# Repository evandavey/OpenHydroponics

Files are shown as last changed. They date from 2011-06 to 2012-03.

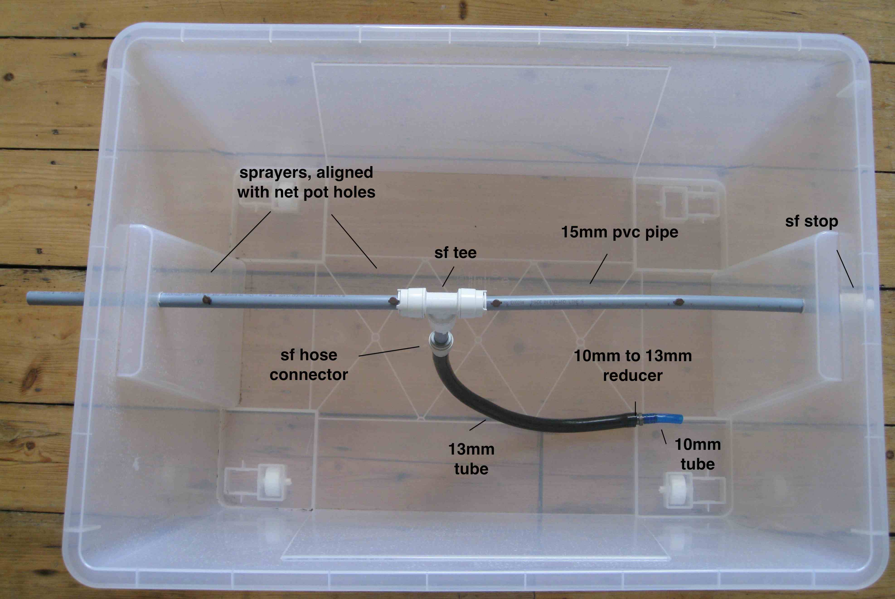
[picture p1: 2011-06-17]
.solderpad/photo.jpg

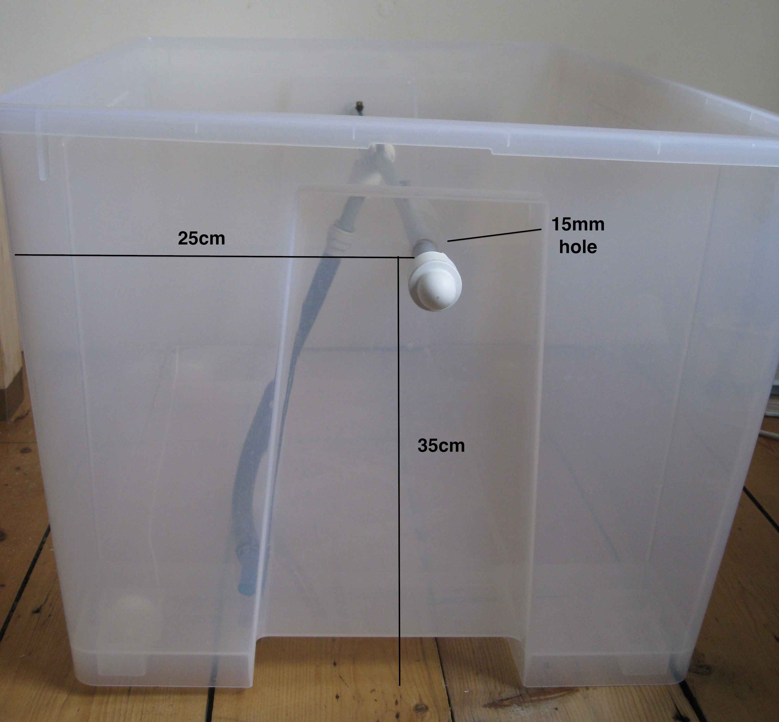
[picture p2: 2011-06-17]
docs/prototype_images/side_w_pipe_hole.jpg

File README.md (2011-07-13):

#OpenHydroponics

An open hardware project for hydroponics.

* firmware
	- arduino pump controller sketch

* hardware
	- Eagle circuit schematic for pump controller

* 3dmodels
	- sketchup model of aeroponics prototype

* docs
	- build documentation for aeroponics prototype

* python
	- python code to interface with the pump controller via serial

* processing
	- processing code to create a gui that interfaces with the conroller via serial

#Contributors

* Evan Davey, evan.j.davey@gmail.com

#License

* See LICENSE.txt

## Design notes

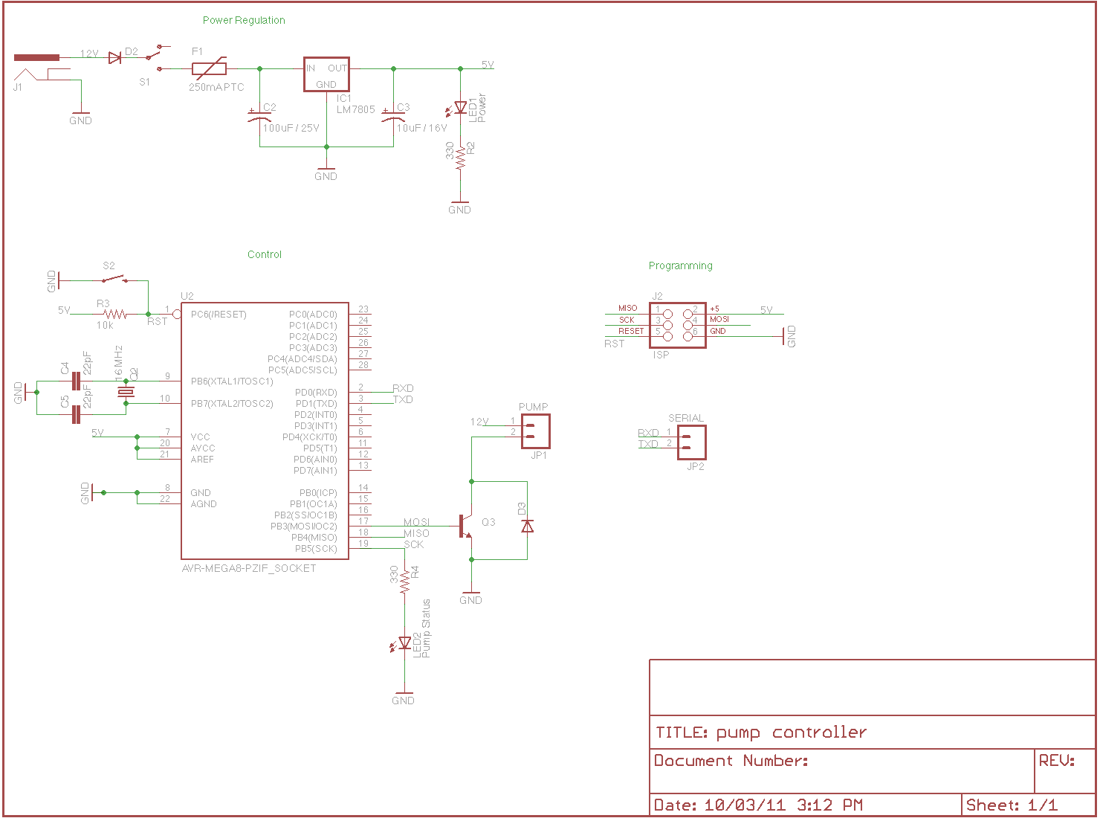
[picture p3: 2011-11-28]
.solderpad/schematic.png

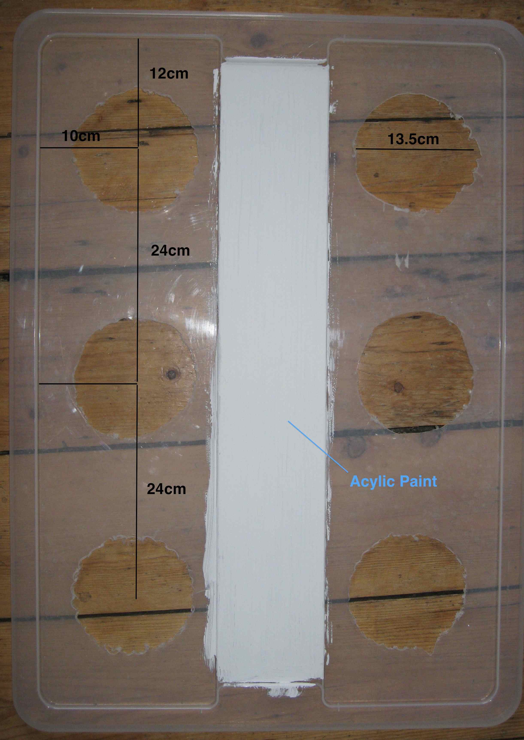
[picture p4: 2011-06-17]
docs/prototype_images/lid_w_annotation.jpg

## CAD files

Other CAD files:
3dmodels/sketchup_aeroponicsmodel.skp

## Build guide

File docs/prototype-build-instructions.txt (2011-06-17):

Title: Aeroponics Prototype System

#Introduction
This document describes how to build an aeroponics system that can be used for indoor growing.

#Why Hydroponics
Hydroponics is a viable alternative to soil-based growing, particularly indoors, for a number of reasons:

* soil is messy indoors
* hydroponics can produce excellent growing results through precise control over plant nutrients
* hydroponics is water-efficient 

There are a number of different hydroponics methods. This build uses aeroponics where the plant's roots are sprayed regularly with a fine mist of nutrient rich solution.  This method can produce excellent results since the spraying process introduces significant oxygen and is targeted directly to the roots.  The downside of the method is that it is more complex and energy inefficient.

#Parts List
* a plastic container with lid, [ikea salma][],[ikea salma lid][]
* approx. 50cm of 13mm irrigation hose, [growing-life][]
* 4 aeroponics spray nozzles, [growing-life][]
* 6 140mm heavy duty net pots, [growing-life][]
* approx. 1m of 15mm pvc pipe, [jw-hinton][]
* 2 sf pvc end caps, [jw-hinton][]
* 1 sf pvc tee connector, [jw-hinton][]
* 1 pvc hose connector, [jw-hinton][]
* 6 15mm sf inserts, [jw-hinton][]
* 1 13mm to 10mm reducer, [water-cooling-shop][]
* approx. 10cm of 10mm hose, [water-cooling-shop][]
* 1 12VDC pump [quality-gadgets-ebay][]

#Build
1. Drill or cut 6x140mm holes in the plastic tub lid.  For the Ikea Salma lid, there are two panels which should have 3 holes each.  They should be placed 10cm from the long edge and at 12cm,36cm and 60cm from the left short edge. 
2. Test that the net pots fit the holes snugly and adjust to fit.
3. Drill a 15mm hole in each side of the tub so that the pvc pipe can be inserted long ways through the tub.  Holes should be 35cm from the bottom and 25cm from the left edge.
4. Cut a 90cm length of pvc pipe and then cut this in half.  Cut a separate 5cm length of pipe.  Insert each end of the pipes into the tee connector using the inserts.  Connect the 5cm pipe to the hose connector then insert into the base of the tee connector. Insert the connected pipe into the plastic tub.  With the lid on, mark the pvc for the best location of the sprayers by aligning them with the net pot holes, drill pilot holes then connect the sprayers.  Place the stop ends on each end of the pvc pipes once the sprayers have been inserted.
5. Cut a small length of 10mm pipe and use this with the  10mm to 13mm reducer to connect to the pump.  Cut a small section of 13mm hose and use this to connect the 13mm reducer end to the hose connector.
6. Fill with a small amount of water then connect the pump directly to the 12v power supply to test.
7. Paint the tub and lid (a primer coat may be required).  This is so light is kept away from the roots / nutrients solution.
8. Move the system to its final location (eg: at a window for sunlight). Fill the tub with a nutrient solution and add a grow medium (eg: perlite) to the net pots. 

[quality-gadgets-ebay]: http://cgi.ebay.co.uk/ws/eBayISAPI.dll?ViewItem&item=190473725204
[water-cooling-shop]: http://www.thewatercoolingshop.co.uk/
[growing-life]: http://www.growing-life.com/
[jw-hinton]: http://www.jwhinton.co.uk/
[ikea salma]: http://www.ikea.com/gb/en/catalog/products/70102972
[ikea salma lid]: http://www.ikea.com/gb/en/catalog/products/90110301

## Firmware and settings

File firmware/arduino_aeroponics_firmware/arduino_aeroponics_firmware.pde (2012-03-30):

/* Hydroponics System 

-- Aeroponics controller
-- Author: Evan Davey, evan.j.davey@gmail.com

--V1.1
--- adds string array for state labels
--- converts data string to json from csv
--- implements a newState variable to allow state change events
--- sends data string on state changes
--- adds a name variable to identify devices

Cycles a pump for use in a hyrdoponics system
Implemented as a state machine 
X-valid serial command 
      *menu -> send main menu
      *data -> send data
      **rst -> state 3 
0-idle 
  Outputs: pumpCtrl=Low,statusLed=Blink,reset=Low
  off timer ends -> state 1
  waterSensor=High -> state 2
  
1-pumping
  Outputs: pumpCtrl=High,statusLed=Low,reset=Low
  on timer ends -> state 1
  waterSensor=High -> state 2
  
2-error,water low
  Outputs: pumpCtrl=Low,statusLed=fast blink,reset=Low
  requires reset to leave this state

3-reset
  Outputs: pumpCtrl=Low,statusLed=Low,reset=High
  Waits delay_time before resetting


*/


// hardware
const int pumpCtrl = 2; //connect via a transistor with back voltage protection
const int statusLed = 13; //connect using a current limiting resistor
const int reset = 12; //connect to reset via a transistor tied to ground
const int waterSensor = 8; //connect to a normally closed float switch
const int manualButton = 3;

// firmware defaults
const float vers=1.1;
char* name="Aeroponics 1";
const unsigned long default_pump_on_time = 30000; //on 30 seconds 
const unsigned long default_pump_off_time = 300000; //off 5 minutes
const long baud_rate=115200; //baud rate for serial 
volatile int debug_mode=0; //when high, outputs status data 
int pumpCycles = 1; //counter of pump cycles
int reset_delay=4; //time to wait after reset command issued
int start_state=0; //starting state
char* stateStrings[]={"0 - Idle","1 - Pumping","2 - Error, Water too low","3 - Waiting to reset","4 - Manual Mode"};
 

// 0 - idle
// 1 - pumping
// 2 - error, water level
// 3 - waiting for reset
volatile int currentState = -1;
volatile int newState = -1;




// Variables will change:
int ledState = LOW;             // ledState used to set the LED
int pumpState = LOW;             // ledState used to set the LED
long pumpTimer = 0; // will store last time LED was updated
int waterSensorState = LOW;
int manualButtonState = LOW;

volatile char cmd='-1';
long pump_on_time; //on 30 seconds 
long pump_off_time; //off 5 minutes
unsigned long previousMillis = 0;
boolean in_menu=false;


void setup() {


  pinMode(pumpCtrl, OUTPUT);
  pinMode(statusLed, OUTPUT);
  pinMode(reset, OUTPUT);
  pinMode(waterSensor, INPUT);
  pinMode(manualButton, INPUT);

  pump_off_time=default_pump_off_time;
  pump_on_time=default_pump_on_time;

  Serial.begin(baud_rate);

  //delay(1000);


  attachInterrupt(1, button1, RISING);

  newState=start_state;


}

void keepTime() {
   //keep the time
  unsigned long currentMillis = millis();
  pumpTimer += currentMillis-previousMillis;
  previousMillis = currentMillis;
  
 
  
}

void mainControlLoop() {
  
  keepTime();
  
  //check for errors
  errorCheck();
  
  //handle state
  handleState();

  
}


void loop()
{

  mainControlLoop();
  
  //in the main menu
  if (in_menu) {
    menu_main();
  }
 
  //process received serial data
  //available command *menu
  handleSerialIn();

  if (debug_mode && !in_menu) {


    if (pumpTimer % 5000 == 0) {
      Serial.println(":: DBEUG ::");
      status_toString();
    }
  } 

}


void handleSerialIn() {


  if ( Serial.available() > 0) { // if there are bytes waiting on the serial port

    char inByte = Serial.read(); // read a byte
    if (inByte == '*') { // if that byte is the desired character

      int len = 5; // expected string is 6 bytes long
      char inString[len]; // declare string variable
      for (int i = 0; i < len; i++) {
        inString[i] = Serial.read();
        delay(100);
      }

      //Serial.println(inString);

      if ( strstr(inString, "menu") != NULL ) { // check to see if the respose is "reset"
          menu_main(); 
      } else if (strstr(inString, "data") != NULL ) {

        //send data
        data_toString();

      } else if (strstr(inString, "*rst") != NULL ) {

        Serial.println("Resetting..");
        //send data
        newState=3;

      } else if (strstr(inString, "sone") != NULL ) {

        //Serial.println("Changing state to 1");
        //send data
        pumpTimer=0;
        newState=1;
        Serial.flush();

      } else if (strstr(inString, "stwo") != NULL ) {

        //send data
        newState=2;
        Serial.flush();

      } else if (strstr(inString,"idle") != NULL ) {

        //send data
        newState=0;
        pumpTimer=0;
        Serial.flush();


     }
    }
  }
}


void state_change() {
 
   data_toString(); 
  
}

void handleState() {
  
  if (newState!=currentState) {
    currentState=newState;
    state_change();
  }

  switch(currentState) {
    //IDLE
  case 0:

    flashLed(statusLed,1,1000);
    digitalWrite(pumpCtrl,LOW);
    //pump off timer exceeded, switch to pumping state
    if (pumpTimer >= pump_off_time) {
      pumpTimer=0;
      pumpCycles++;
      newState=1;
    }
    break;

    //PUMPING
  case 1:


    digitalWrite(pumpCtrl,HIGH);
    //pump on timer exceeded, switch to idle state
    if (pumpTimer >= pump_on_time) {
      pumpTimer=0;
      newState=0;
    }
    break;
    
 
    //ERROR
  case 2:
    digitalWrite(pumpCtrl,LOW);
    flashLed(statusLed,3,100);
    break;

    //RESET
  case 3:
  
   
    
    for (int i=reset_delay;i>0;i--) {
      Serial.print("Will reset in ");
      Serial.print(i);
      Serial.println("s");
      delay(1000);
    }
    
    Serial.println("** Resetting now **");
    digitalWrite(reset,HIGH);
    newState=0;
    break;

  //MANUAL ON
 
   case 4:
    digitalWrite(pumpCtrl,HIGH);
    break;

  default:
    break;

  }      


}

void data_toString() {


  
  
  //delay(1000);
  Serial.print("{");
  
  Serial.print("\"State\"");
  Serial.print(":");
  Serial.print(currentState);
  Serial.print(",");
  
   Serial.print("\"State Description\"");
  Serial.print(":");
  Serial.print(stateStrings[currentState]);
  Serial.print(",");
  
  Serial.print("\"Pump Timer\"");
  Serial.print(":");
  Serial.print(pumpTimer/1000);
  Serial.print(",");
  
  Serial.print("\"Pump Off Time\"");
  Serial.print(":");
  Serial.print(pump_off_time);
  Serial.print(",");
  
  Serial.print("\"Pump On Time\"");
  Serial.print(":");
  Serial.print(pump_on_time);
  Serial.print(",");
  
  Serial.print("\"Pump Cycles\"");
  Serial.print(":");
  Serial.print(pumpCycles);
  Serial.print(",");
  
  Serial.print("\"Water Sensor\"");
  Serial.print(":");
  Serial.print(waterSensorState);
  Serial.print(",");
  
  Serial.print("\"Name\"");
  Serial.print(":");
  Serial.print("\"");
  Serial.print(name);
  Serial.print("\"");
  Serial.print(",");

  Serial.print("}");
  
  Serial.println("");


}


void errorCheck() {

  // water level too low, enter error state
  if (!checkWater()) {
    newState=2; 
    return;
  } 





}


//checks the water sensor and returns true if water is present
boolean checkWater() {

/*  waterSensorState=digitalRead(waterSensor);

  if (waterSensorState == HIGH) {
    return false;
  } 
  else {
    return true;
  }
 
*/
 return true;

}

void state_toString(int state) {

  
  Serial.println(stateStrings[state]);
 

}

void status_toString() {

  Serial.print("Version: ");
  Serial.println(vers);
  Serial.print("Debug Mode: ");
  Serial.println(debug_mode);
  Serial.print("State: ");
  state_toString(currentState);
  Serial.print("Pump Timer: ");
  Serial.println(pumpTimer/1000);
  Serial.print("Pump Cycles: ");
  Serial.println(pumpCycles);
  Serial.print("Pump Off Time: ");
  Serial.println(pump_off_time/1000);
  Serial.print("Pump On Time: ");
  Serial.println(pump_on_time/1000);
  Serial.print("Water Sensor: ");
  Serial.println(waterSensorState); 

}

void menu_show() {

  Serial.println("::::: HYDRO SYSTEM :::::");
  status_toString();
  delay(500);
  Serial.println("--------------------------------");
  Serial.println("(1) - exit menu");
  Serial.println("(2) - reset");
  Serial.println("(3) - toggle debug");
  Serial.println("(4) - force state");
  Serial.println("(5) - set pump on time");
  Serial.println("(6) - set pump off time");

}

void menu_main() {


  //first time in, show the menu
  if (!in_menu) {
    delay(700);
    Serial.flush();
    menu_show();
    in_menu=true;
  }


  //wait for command
  if (in_menu) {

    if ( Serial.available() > 0) { // if there are bytes waiting on the serial port

      cmd = Serial.read();

      switch (cmd) {

      case '1':
        Serial.println("exiting menu");
        in_menu=false;
        break;

      case '2':

        in_menu=false;
        newState=3;
        break;

      case '3':
        in_menu=false;
        debug_mode=!debug_mode;
        Serial.print("Debug mode=");
        Serial.println(debug_mode);
        break;

      case '4':


        Serial.println("States-");
        for (int i=0;i<=3;i++) {
          state_toString(i);
        }
        Serial.print("State Number (0-3): ");

        Serial.flush();
        while (true) {
          //ensure operation continues while waiting
          mainControlLoop();
          if ( Serial.available() > 0) { // if there are bytes waiting on the serial port
            char * cmd_c="0";
            cmd_c[0]=Serial.read();

            int cmd_i=atoi(cmd_c);

            if (cmd_i<=3) {
              Serial.print("Setting state to: ");
              Serial.println(cmd_i);
              pumpTimer=0;
              newState=cmd_i;
              in_menu=false;
              break;
            } 
            else {

              Serial.print("State Number (0-3): ");
              Serial.flush();
            }
          } 

        }
        break;

      case '5':
        
        Serial.println("(1) 10 seconds");
        Serial.println("(2) 20 seconds");
        Serial.println("(3) 30 seconds");
        Serial.println("(4) 60 seconds");
        Serial.println("(5) 120 seconds");

        Serial.flush();
        while (true) {
          //ensure operation continues while waiting
          mainControlLoop();
          int t;
          if ( Serial.available() > 0) { 
            cmd=Serial.read();

           
            switch(cmd) {

            case '1':
              t=10;
              break;
            case '2':
              t=20;
              break;
            case '3':
              t=30;
              break;
            case '4':
              t=60;
              break;
            case '5':
              t=120;
              break;
            default:
              t=30;
            }
            
          pump_on_time=t*1000;
          Serial.print("new pump time:") ;
          Serial.println(t); 
          in_menu=false;
          break; 

          } 
         
        }  
        break;
      
      case '6':
        
        Serial.println("(1) 60 seconds");
        Serial.println("(2) 2 minutes");
        Serial.println("(3) 5 minutes");
        Serial.println("(4) 10 minutes");
        Serial.println("(5) 15 minutes");

        Serial.flush();
        while (true) {
          //ensure operation continues while waiting
          mainControlLoop();
          long t;
          if ( Serial.available() > 0) { 
            cmd=Serial.read();

           
            switch(cmd) {

            case '1':
              t=60;
              break;
            case '2':
              t=120;
              break;
            case '3':
              t=300;
              break;
            case '4':
              t=600;
              break;
            case '5':
              t=900;
              break;
            default:
              t=300;
            }
            
          pump_off_time=t*1000;
         
        
          Serial.print("new pump time:") ;
          Serial.println(t); 
          in_menu=false;
          break; 

          } 
         
        }  
        break;   
      default:
        Serial.println("illegal command");
        Serial.flush();
        menu_show(); 

      }

    }
  }



}


//blinks a Led pin numBlinks at the blinkRate 
void flashLed(int ledPin,int numBlinks,int blinkRate) {


  digitalWrite(ledPin,LOW);
  for (int i=1;i<=numBlinks;i++) {

    digitalWrite(ledPin,HIGH);
    delay(blinkRate);
    digitalWrite(ledPin,LOW);
    delay(blinkRate);

  }

}  

void button1() {
 
  static unsigned long last_interrupt_time = 0;
  unsigned long interrupt_time = millis();
  // If interrupts come faster than 200ms, assume it's a bounce and ignore
  if (interrupt_time - last_interrupt_time > 200)
  {
   manualButtonState = !manualButtonState;
 
 if (manualButtonState) {
   
    newState=4; 
 }
 else {
    newState=0; 
 }
  }
  last_interrupt_time = interrupt_time;
 
  
}

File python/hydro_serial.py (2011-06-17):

import serial
import os
import time

port='usbserial-A800csiR'
#port='usbmodem3d11'
#port='usbmodem1d11'


ser = serial.Serial('/dev/tty.'+port, 115200, timeout=1)

alarm_sent=False
while 1:

    ser.write('*data')
    line = ser.readline().strip()

    header=line.split(",")

    #header received
    if header[0]=='State':
        line=ser.readline().strip()
        data=line.split(",")

        if data[0]=='2':
            if not alarm_sent:
                print 'Hydro error'
                os.system('growlnotify -m "Hydroponics: Water too low"')
                alarm_sent=True


        for x in range(0,len(data)):
            print header[x] + ":" + data[x]
    
        time.sleep(5)

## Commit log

2011-03-10 Version 1.0, Initial Checkin
    [eaglecircuit_pumpcontroller.sch]
2011-03-26 Added sketchup 3d model
    [sketchup_aeroponicsmodel.skp]
2011-06-17 Updated firmware to operate as a state machine. Adds serial data control / feedback. Supports remote reset and water monitoring
    [sketch_pumpcontrol.pde]
2011-06-17 naming restructure
    [eaglecircuit_pumpcontroller.sch, sketchup_aeroponicsmodel.skp]
2011-11-28 added .solderpad files
